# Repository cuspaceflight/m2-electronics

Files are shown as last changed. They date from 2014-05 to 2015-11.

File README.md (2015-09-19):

# Martlet 2 Flight Computers

This repository contains the schematics, PCB designs and firmware for the
various electronic systems onboard Martlet 2.

## M2FC: Flight Computer
This PCB records sensor data to onboard storage and determines when to fire
pyrotechnic channels for staging and parachute release.

## M2R: Radio
This PCB receives GPS signals and transmits rocket telemetry (lat, lng, alt, 
max alt) over a satellite radio and 70cm radio link.

## Radio Link M2RL
Communicate between two M2FCs

## Firmware
### ChibiOS Instructions

```bash
$ git submodule update --init
$ cd ChibiOS/ext
$ unzip fatfs-0.9-patched.zip
$ cd ../os/various/fatfs_bindings
$ sed -i '/extern SDCDriver SDCD1;/d' fatfs_diskio.c
```

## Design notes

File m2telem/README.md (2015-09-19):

# M2 Telemetry Common Code

Functions to encode and decode M2 telemetry packets, and to transmit and 
receive framed packets.

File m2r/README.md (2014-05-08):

# Martlet 2 Radio Board

This PCB transmits rocket telemetry (lat, lng, alt, max alt) over a satellite
radio and 70cm radio link.

The satellite radio uses a RockBLOCK Iridium modem. The 70cm link will use an
NTX2b from Radiometrix with a standard 1/4 wave antenna, in a similar setup to
the usual HAB case.

There's some possibility for clever radio modes and coding to be used, but it
will depend on how much time is available.

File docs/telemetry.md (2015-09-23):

# Martet 2 Telemetry

Document version: 2.0

This document describes version 2 of the Martlet 2 telemetry packet format. 
Compared to version 1, the two halves (the data segment and the metadata 
segment) are switched, to accommodate a trailing checksum. The packet mode 
became _managed_, associated with a particular channel, rather than being 
specified in the packet itself. Origins and channel constants are unchanged.

## Packet Format

16 byte packets: 8 byte data, 8 byte footer.

    [  0  | DATA       ]\
    [  1  | DATA       ] |
    [  2  | DATA       ] |
    [  3  | DATA       ] |- User data. Might be an 8-char string or an int64 or
    [  4  | DATA       ] |  two floats or four int16s or whatever else MODE
    [  5  | DATA       ] |  indicates.
    [  6  | DATA       ] |
    [  7  | DATA       ]/
    [  8  | TIMESTAMP  ]\
    [  9  | TIMESTAMP  ] |- A 32 bit unsigned timestamp that runs at the system
    [ 10  | TIMESTAMP  ] |  clock frequency so will overflow fairly often.
    [ 11  | TIMESTAMP  ]/
    [ 12  | METADATA   ]--- Origin of data and reserved bits.
    [ 13  | CHANNEL    ]--- Data channel.
    [ 14  | CHECKSUM L ]\
    [ 15  | CHECKSUM U ]/-- Verify packet contents.

## Metadata

The metadata byte describes the original source of a telemetry packet in the 
lower four bits. The upper four bits are reserved.

### Packet Origins

    0   RESERVED
    1   M2FC BODY
    2   M2FC NOSE
    3   M2R
    F   Groundstation

## Channel

The channel byte describes what data this packet contains. The `mode`
referenced in the channel table refers to one of the data formats described in
the `Data` section.

### Packet Channels

    Channel  Mode  Description
    -------------------------------------------------------------
    0x0            SYSTEM
       0     0      Initialisation message, contains the origin string
       1     0      Firmware version, as Git commit hash
       2     8      Statistics: [CPU_usage uSD_duty 0 0 0 0 0 0 0]
       3     8      Status 1: [M2FCBODY M2FCNOSE M2R 0 0 0 0 0]
       4     8      Status 2: [ADC LG_Accel HG_Accel Baro Gyro Magno Pyro uSD]
       5     8      Status 3: [SE MC Datalogging Config 0 0 0 0]
       6     8      Status 4: [RockBLOCK Radio GPS 0 0 0 0 0]

    0x1            CALIBRATION
       0     4      Timestamp frequency  [f 0]
       1     5      Low-G accelerometer  [axis gravity-magnitude 0 0]
       2     5      High-G accelerometer [axis gravity-magnitude 0 0]
       3     6      Barometer            [d0 c1 c2 c3]
       4     6      Barometer            [c4 c5 c6 d7]

    0x2            INTERTIAL MEASUREMENT
       0     5      Low-G accelerometer  [x y z 0]
       1     5      High-G accelerometer [x y z 0]
       2     3      Barometer            [pressure temperature]
       3     5      Rate gyroscope       [x y z 0]
       4     5      Magnetometer         [x y z 0]

    0x3            EXTERNAL SENSORS
       0     5      Battery voltage [millivolts 0 0 0]
       1     5      Strain gauges   [ch1 ch2 ch3 0]
       2     5      Thermocouples   [ch1 ch2 ch3 0]

    0x4            STATE MACHINES
       0     3      Mission Control [old_state new_state]

    0x5            STATE ESTIMATION
       0     9      Prediction output  I     [dt       height]
       1     9      Prediction output II     [velocity acceleration]
       2     9      Pressure measurement     [sensor   estimate]
       3     9      Acceleration measurement [sensor   estimate]

    0x6            PYROTECHNICS
       0     5      Continuity results [ch1 ch2 ch3 0]
       1     5      Fired              [ch1 ch2 ch3 0]

    0x7            LOCATION
       0     8      GPS Time       [year_l year_h month day hour min sec valid]
       1     3      GPS Position   [latitude longitude]
       2     3      GPS Altitude   [height height_msl]
       3     7      GPS Status     [fix_type flags num_sv 0 0 0 0 0]

;qa
## Checksum

CRC16-CCITT with polynomial 0x1021 and initial value 0xFFFF, no 
post-processing. Stored little-endien.

## Data

Data formatting depends on channel, allocated in the channel table. Multi byte 
entries are stored little-endien.

### Packet Modes

    Mode  Type      Format   Description
    -------------------------------------------------------------
     0    char*      s8       Eight byte string
     1    int64_t    q        64 bit signed integer
     2    uint64_t   Q        64 bit unsigned integer
     3    int32_t    ii       Two 32bit signed integers
     4    uint32_t   II       Two 32bit unsigned integers
     5    int16_t    hhhh     Four 16bit signed integers
     6    uint16_t   HHHH     Four 16bit unsigned integers
     7    int8_t     bbbbbbbb Eight 8bit signed integers
     8    uint8_t    BBBBBBBB Eight 8bit unsigned integers
     9    float      ff       Two 32bit single precision floats
     10   double     d        One 64bit double precision float

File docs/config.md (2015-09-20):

# Martlet 2 Config Files

Configuration settings are saved in a file named `config.txt` in the root of 
the SD card. Each line is one `key=value` pair, with values interpreted as 
either integers or floating point numbers. Bools should be specified as 0 or 1. 
Ints are all unsigned (in other words, non-negative, >= 0).

Configuration keys must be *in order* and exactly as follows:

Key              | Type  | Description
-----------------|-------|-----------------------------------------------------
accel_axis       | Int   | Which accelerometer axis is 'up', 0=x 1=y 2=z
pyro_firetime    | Int   | Time in milliseconds to fire pyros
pyro_1           | Int   | Pyro channel 1 usage: 0=unused 1=drogue 2=main
pyro_2           | Int   | Pyro channel 2 usage: 0=unused 1=drogue 2=main
pyro_3           | Int   | Pyro channel 3 usage: 0=unused 1=drogue 2=main
ignition_accel   | Int   | Acceleration threshold for detecting motor ignition, in m/s/s
burnout_time     | Int   | Time limit on motor burn duration, in milliseconds
apogee_time      | Int   | Time since burnout after which apogee is considered to have been reached, in milliseconds
main_altitude    | Int   | Altitude below which to release the main parachute, in metres AGL
main_time        | Int   | Time since apogee at which to release the main parachute, in milliseconds
landing_time     | Int   | Time since apogee at which to consider the rocket landed, in milliseconds
use_adc          | Bool  | 1 to read the ADCs, 0 to disable
use_magno        | Bool  | 1 to read the magno, 0 to disable
use_gyro         | Bool  | 1 to read the gyro, 0 to disable

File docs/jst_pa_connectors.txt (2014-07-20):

HEADER

02 SIDE S02B-PASK-2 1830747
03 SIDE S03B-PASK-2 1830748
04 SIDE S04B-PASK-2 1830749     RS: 512-8484

02 TOP  B02B-PASK   1830733
03 TOP  B03B-PASK   1830735
04 TOP  B04B-PASK   1830737

HOUSING

02 PAP-02V-S        1830726
03 PAP-03V-S        1830728
04 PAP-04V-S        1830729

CRIMP PIN

SPHD-001T-P0.5                  RS: 688-1381

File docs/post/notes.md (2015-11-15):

# M2 Electronics Postmortem Documentation: Planning Notes

## Structure

1. Introduction, Scope, Objectives
1. Hardware Design Review
1. Hardware Manufacture Review
1. Firmware Design Review
1. Firmware Implementation Review
1. Performance Analysis
1. Bugs and Other Issues
1. Lessons Learnt & Recommendations
1. Conclusions

## Structure Take 2

1. Summary
    1. Brief overview
    1. Key successes
    1. Key problems
    1. Key takeaways
1. Introduction
    1. Martlet 2 Overview
    1. Report scope and goals
    1. Project objectives
1. Avionics Overview
    1. Custom Hardware
        1. M2FC
        1. M2R
        1. M2RL
        1. M2PA
        1. JOEY Tracker
    1. Other Electronics
        1. RockBLOCK
        1. PerfectFlite
        1. Cameras
    1. Other Components
        1. Metrons
        1. Strain gauges
        1. Thermocouples
        1. Battery cases
        1. Arming switches
        1. Status LEDs
        1. Antennas
    1. Interconnection
1. Project Management
    1. Time management
    1. Collaboration
    1. Prioritisaton and Feature Freeze
1. System Review
1. Hardware Review
    1. Technology Choices (KiCAD)
    1. Design Procedure
    1. M2FC
        1. Analogue
        1. Pyrotechnics
        1. IMU
        1. SD Card
        1. Off-board integrations
    1. M2R
        1. Radio
        1. GPS
        1. RockBLOCK
        1. Buzzer
    1. M2RL
    1. M2PA
    1. Arming System
    1. Power System
    1. Other Electronics
        1. RockBLOCK
        1. PerfectFlite
        1. Cameras
    1. Other Components
        1. Metrons
        1. Strain gauges
        1. Thermocouples
        1. Battery cases
        1. Arming switches
        1. Status LEDs
        1. Antennas
    1. Interconnections
        1. JST PA
        1. Spec 55
        1. Radio links
    1. Manufacture
        1. Issues Encountered
    1. Testing
1. Software Review
    1. Technology Choices (C, git, ChibiOS)
    1. Reliability Management
        1. Watchdogs
        1. Hardware error handling
    1. Drivers
    1. Calibration
    1. Flight state machine
        1. Safety Timeouts
        1. Ignition Detection
    1. Status reporting and collection
    1. Telemetry collection and forwarding/storage
    1. Software interfaces
    1. Testing
    1. Ground station software
    1. Revision Control / Release Process
1. Integration Review
    1. Mounting
    1. Enclosures
    1. Switches and LEDs
    1. Cameras
    1. Antennas
    1. Cabling
    1. Sensors
1. Launch Retrospective
    1. Missing Features
        1. IMU Magno/Gyro
        1. ADC recording
        1. M2RL
    1. Asssembly
    1. Performance
        1. Radio
        1. Datalogging
        1. Sensors
        1. State estimation
    1. Issues Encountered
        1. No RockBLOCK signal while in enclosure
        1. Accidental body Metron firing in assembly
        1. Arming switch high up
        1. Arming switch behind launch rail
        1. Radio not enabled, requiring reprogramming
        1. Key breaking apart
        1. Keyswitch breaking off
        1. LED breaking off
        1. Upright on arming requirement
        1. No safety timeout
        1. Sensitive ignition detection
        1. Early body Metron firing while on pad
        1. SD cards lost
1. Conclusions & Recommendations

## Thoughts To Include
Per section: Overview, Performance, Issues, Lessons Learnt

## Links

GitHub repo: https://github.com/cuspaceflight/m2-electronics
Photos: https://www.flickr.com/photos/randomskk/albums/72157645881007740

## Thoughts drop

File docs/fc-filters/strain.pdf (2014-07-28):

## Filter Wizard

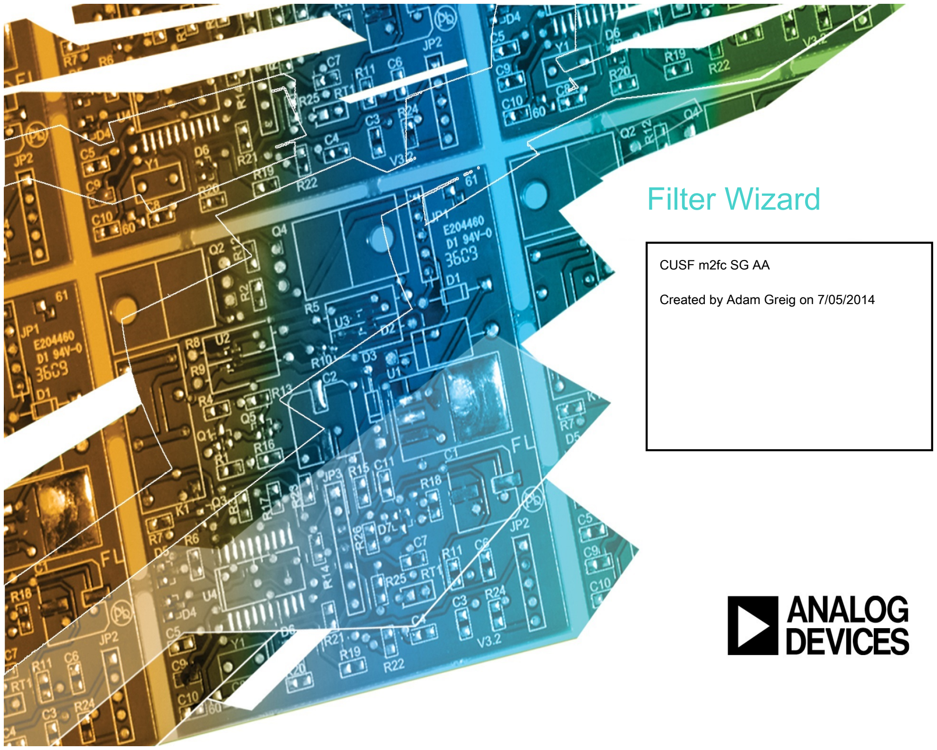
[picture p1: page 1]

CUSF m2fc SG AA

Created by Adam Greig on 7/05/2014

## Filter Wizard Design Report

Filter Requirements for Low-Pass, 4th order Butterworth Specifications: Optimize for Noise, +Vs= 3.3, -Vs= 0
Gain: 0 dB
Passband: -3dB at 2kHz
Stopband: -55dB at 10kHz
Component Tolerances: Capacitor = 10%; Resistor = 1%; Inductor = 5%; Op Amp GBW = 20% BOM: refer to BOM.csv file

Magnitude(dB)

Magnitude(Volts per Volt)

Phase(degrees)

Phase(radians)

Group Delay

Phase Delay

Step Response

Noise

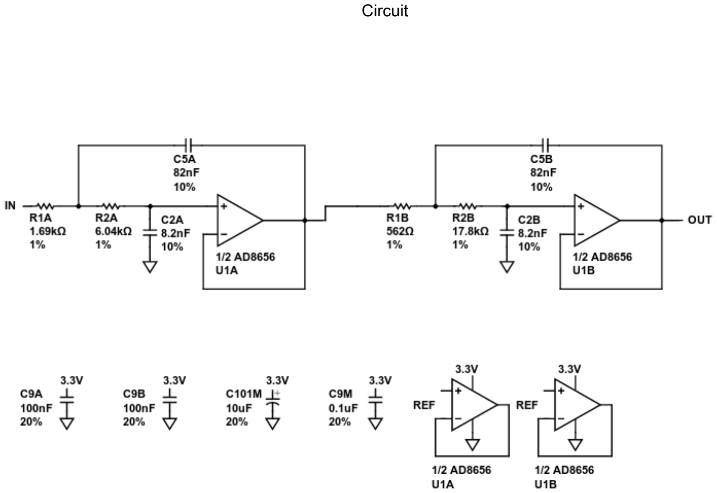
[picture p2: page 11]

Circuit

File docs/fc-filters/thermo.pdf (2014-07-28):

## Filter Wizard

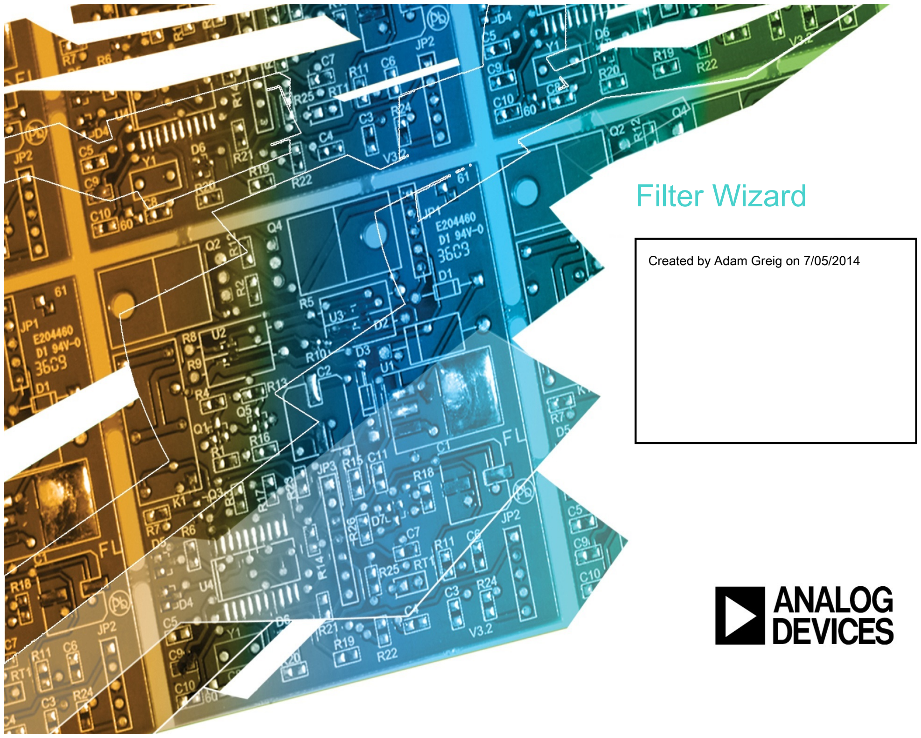
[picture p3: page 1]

Created by Adam Greig on 7/05/2014

## Filter Wizard Design Report

Filter Requirements for Low-Pass, 4th order Butterworth Specifications: Optimize for Specific Components, +Vs= 3.3, -Vs= 0 Gain: 0 dB
Passband: -3dB at 300Hz
Stopband: -40dB at 1kHz
Component Tolerances: Capacitor = 5%; Resistor = 1%; Inductor = 5%; Op Amp GBW = 20% BOM: refer to BOM.csv file

Magnitude(dB)

Magnitude(Volts per Volt)

Phase(degrees)

Phase(radians)

Group Delay

Phase Delay

Step Response

Noise

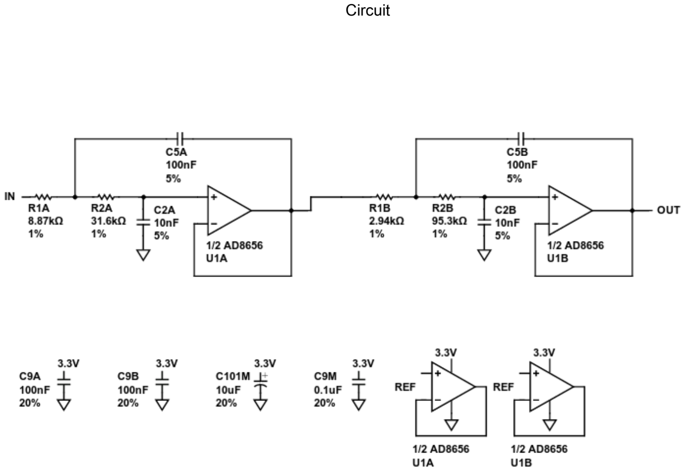
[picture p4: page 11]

Circuit

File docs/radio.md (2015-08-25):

# Martlet 2 Radio Protocol

Document version: 1.1

This document describes the physical and data link level radio protocol for 
Martlet 2. See the telemetry documentation for description of the application 
layer data packets.

## Physical Layer

Martlet 2 is equipped with a FSK radio module whose carrier frequency is 
controlled by the input voltage. However its primary telemetry downlink is via 
BPSK data, with a CW/Morse identification mode.

### Telemetry Downlink Mode

While downlinking telemetry packets, the following settings apply:

-                               |- 
--------------------------------|---------------
Nominal Carrier Frequency       | 434.650MHz
Modulation                      | BPSK
Bit rate                        | 2000 bps

### Identification Mode

In compliance with FCC 97.119 b 3, Martlet 2 will also identify itself and its 
data mode by a CW transmission, repeated twice. The transmitted message is:

    AD6AM/AM AD6AM/AM MARTLET 2 CUSF.CO.UK/M2R

-                               |-
--------------------------------|---------------
Nominal Carrier Frequency       | 434.650MHz
Modulation                      | Morse OOK
Speed                           | 20 wpm

## Data Link Layer

16 byte application packets are first randomised by combining with an LFSR of 
polynomial `x^8 + x^6 + x^4 + x^3 + x^2 + x^1 + 1`. This ensures sufficient 
transitions in the transmitted data stream and aids in balancing the 
transmitted spectrum. For further details see CCSDS 231.0-B-2 section 5.

Randomised application packets are then encoded with the systematic (256,128) 
LDPC code specified in CCSDS 231.1-O-1. The resulting codewords are transmitted 
left bit first, which corresponds to the most significant bit in the lowest 
(first) byte of the application payload.

Each codeword is then prefixed with the 16 bit synchronisation pattern 
`1110101110010000`, transmitted left bit first.

## Radio Sequencing

The radio follows this sequence on power-up:

1. Carrier enabled
2. If necessary, radio enters identification mode and repeats identification 
   message two times. Identification occurs once on startup and at least every 
   ten minutes thereafter.
3. Radio transitions to telemetry downlink mode and transmits a brief 
   unmodulated carrier.
4. Carrier modulated with repeating 1010 preamble for 16 bit periods
5. Data frame transmitted, starting with leading 1 in synchronisation pattern,
   ending with final (rightmost) parity bit of codeword.
6. Up to fifteen further frames transmitted starting with synchronisation 
   pattern, with no additional preamble.
7. Go to (2).

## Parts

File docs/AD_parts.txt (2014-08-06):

PART                QTY COST    SAMPLED

ADP3335ARMZ-3.3RL7  3   1.07
ADP3338AKCZ-5-R7    1   2.24
ADUM1201CRZ         5   2.85    2 SAMPLED 2014-08-04
ADUM5201CRWZ        2   8.80    2 SAMPLED 2014-07-20
ADL5324ARKZ-R7      1   7.28    2 SAMPLED 2014-07-20
ADXL375BCCZ         2   7.45    2 SAMPLED 2014-07-20
ADXL345BCCZ         2   5.97    1 SAMPLED 2014-08-03
AD8226ARMZ          6   2.45    1 SAMPLED 2014-08-03, 2 SAMPLED 2014-08-04
AD8541AKSZ-REEL7    6   0.64
AD8656ARMZ          12  2.72    1 SAMPLED 2014-08-03, 2 SAMPLED 2014-08-04
AD8495CRMZ          6   6.52    2 SAMPLED 2014-07-20, 1 SAMPLED 2014-08-03 (BACKORDER TIL SEPT 9), 2 SAMPLED 2014-08-04

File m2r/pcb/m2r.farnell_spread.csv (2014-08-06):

number | comment | name | stock | price | qty | cost | url
2141424 | 2 m2r:R0402 R3 | MULTICOMP - MC00625W040212R0 - RESISTOR, 2R, 0.063W, 1%, 0402 | 8,075 | 0.022 | 1 | 0.022 | http://onecall.farnell.com/_/_/_/dp/2141424
2063945 | 8M m2r:HC49S X10 | FOX ELECTRONICS - FOXSLF/080-20 - CRYSTAL, 8.0MHZ, 20PF | 683 | 0.32 | 1 | 0.32 | http://onecall.farnell.com/_/_/_/dp/2063945
1608592 | SMA m2r:SMA-142-0701-801 P7 | EMERSON CONNECTIVITY/JOHNSON - 142-0701-801 - RF COAXIAL, SMA, STRAIGHT JACK, 50OHM | 125 | 4.94 | 1 | 4.94 | http://onecall.farnell.com/_/_/_/dp/1608592
2211068 | 10µ m2r:C1206 C18 | TDK - CGA5L1X7R1E106K160AC - CAP, MLCC, X7R, 10UF, 25V, 1206 | 953 | 0.65 | 1 | 0.65 | http://onecall.farnell.com/_/_/_/dp/2211068
2333614 | 6k8 m2r:R0603 R6 | BOURNS - CR0603-FX-6801ELF - RESISTOR THICK FILM, 6.8KOHM, 1%, 0603 | 1,463 | 0.018 | 1 | 0.018 | http://onecall.farnell.com/_/_/_/dp/2333614
BT01732 | BAT BOX None X1 | BULGIN - BX0027 - BATTERY HOLDER ENCLOSED FOUR X AA | 75 | 6.72 | 1 | 6.72 | http://onecall.farnell.com/_/_/_/dp/BT01732
2290330 | YELLOW m2r:LED0603 D3 D4 D6 D5 | KINGBRIGHT - KP-1608SYCK - LED, 0603, 150MCD, YELLOW | 15,179 | 0.054 | 4 | 0.216 | http://onecall.farnell.com/_/_/_/dp/2290330
2290329 | RED m2r:LED0603 D1 D2 | KINGBRIGHT - KP-1608SURCK - LED, 0603, 230MCD, RED | 65,670 | 0.054 | 2 | 0.108 | http://onecall.farnell.com/_/_/_/dp/2290329
2331989 | 100 m2r:R0603 R14 R8 R9 R7 R10 R12 R11 R13 R5 R4 | TE CONNECTIVITY - CRGH0603F100R - RESISTOR, POWER, 100R, 0.2W, 1%, 0603 | 4,737 | 0.008 | 10 | 0.08 | http://onecall.farnell.com/_/_/_/dp/2331989
2099794 | ADL5324 m2r:SOT89-3 IC7 | ANALOG DEVICES - ADL5324ARKZ-R7 - RF, AMP, 400MHZ-4GHZ, 0.5W, SOT89 | 834 | 7.28 | 1 | 7.28 | http://onecall.farnell.com/_/_/_/dp/2099794
1885332 | 10p m2r:C0402 C19 | JOHANSON TECHNOLOGY - 500R07S100GV4T - CAP, RF, C0G/NP0, 10PF, 50V, 0402 | 10,465 | 0.235 | 1 | 0.235 | http://onecall.farnell.com/_/_/_/dp/1885332
1885324 | 6p2 m2r:C0402 C22 | JOHANSON TECHNOLOGY - 500R07S6R2CV4T - CAP, RF, C0G/NP0, 6.2PF, 50V, 0402 | 4,870 | 0.113 | 1 | 0.113 | http://onecall.farnell.com/_/_/_/dp/1885324
1830729 | HOUSING None X5 X6 X7 | JST (JAPAN SOLDERLESS TERMINALS) - PAP-04V-S - HOUSING, CRIMP, RECEPTACLE, 2MM, 4WAY | 37,852 | 0.10 | 3 | 0.30000000000000004 | http://onecall.farnell.com/_/_/_/dp/1830729
2368169 | CGA0402MLC-12G m2r:R0402 D8 D7 D9 D10 D11 | BOURNS - CGA0402MLC-12G - ESD SUPPRESSOR, 0402, 12V, 0.2PF | 8,890 | 0.138 | 5 | 0.6900000000000001 | http://onecall.farnell.com/_/_/_/dp/2368169
2331727 | 1k m2r:R0603 R2 | TE CONNECTIVITY - CRGH0603J1K0 - RESISTOR, POWER, 1K0, 0.2W, 5%, 0603 | 2,100 | 0.006 | 1 | 0.006 | http://onecall.farnell.com/_/_/_/dp/2331727
1078200 | ADuM1201 m2r:SOIC8 IC5 IC3 IC4 | ANALOG DEVICES - ADUM1201ARZ - DIGITAL ISOLATOR, 2CH, 150NS, SOIC8 | 999 | 2.46 | 3 | 7.38 | http://onecall.farnell.com/_/_/_/dp/1078200
2285660 | 5n6 m2r:L0402 L3 | COILCRAFT - 0402CS-5N6XGLU - INDUCTOR, RF, 5.6NH, 2%, 4.8GHZ, SMD | 296 | 0.894 | 1 | 0.894 | http://onecall.farnell.com/_/_/_/dp/2285660
1759055 | 15p m2r:C0603 C35 C36 | MULTICOMP - MC0603N150J500CT - CAP, MLCC, C0G/NP0, 15PF, 50V, 0603 | 47,738 | 0.008 | 2 | 0.016 | http://onecall.farnell.com/_/_/_/dp/1759055
2112704 | 10n m2r:C0603 C17 | TDK - C1608C0G1E103J - CAP, MLCC, C0G/NP0, 10NF, 25V, 0603 | 3,907 | 0.133 | 1 | 0.133 | http://onecall.farnell.com/_/_/_/dp/2112704
1885343 | 20p m2r:C0402 C21 C20 | JOHANSON TECHNOLOGY - 500R07S200GV4T - CAP, RF, C0G/NP0, 20PF, 50V, 0402 | 6,525 | 0.054 | 2 | 0.108 | http://onecall.farnell.com/_/_/_/dp/1885343
1830726 | HOUSING None X3 X4 X9 | JST (JAPAN SOLDERLESS TERMINALS) - PAP-02V-S - HOUSING, CRIMP, RECEPTACLE, 2MM, 2WAY | 24,617 | 0.107 | 3 | 0.321 | http://onecall.farnell.com/_/_/_/dp/1830726
1142488 | RG LED None X8 | KINGBRIGHT - L-937EGW - LED, 3MM, HE-RED/GRN | 24,541 | 0.33 | 1 | 0.33 | http://onecall.farnell.com/_/_/_/dp/1142488
2285957 | 120n m2r:L0603 L1 | COILCRAFT - 0603CS-R12XGLU - INDUCTOR, RF, 120NH, 2%, 1.3GHZ, SMD | 83 | 0.64 | 1 | 0.64 | http://onecall.farnell.com/_/_/_/dp/2285957
1865153 | ALM-2712 m2r:ALM-2712 IC9 | AVAGO TECHNOLOGIES - ALM-2712-BLKG - FILTER, FRONT END, LNA/GPS, 12MCOB | 129 | 2.09 | 1 | 2.09 | http://onecall.farnell.com/_/_/_/dp/1865153
2376929 | ADP3333 m2r:MSOP8 IC11 | ANALOG DEVICES - ADP3333ARMZ-2.5-R7 - 300MA FIXED ANYCAP LDO | 859 | 1.24 | 1 | 1.24 | http://onecall.farnell.com/_/_/_/dp/2376929
1651284 | ADP3338 m2r:SOT223 IC1 | ANALOG DEVICES - ADP3338AKCZ-5-R7. - LDO REG, 1A, RECISION 5V, SOT223 | 507 | 2.24 | 1 | 2.24 | http://onecall.farnell.com/_/_/_/dp/1651284
2285968 | 1n6 m2r:L0603 L2 | COILCRAFT - 0603CS-1N6XJLU - INDUCTOR, RF, 1.6NH, 5%,12.5GHZ, SMD | 210 | 0.505 | 1 | 0.505 | http://onecall.farnell.com/_/_/_/dp/2285968
1830747 | CONN_2 m2r:S02B-PASK-2 P1 P8 P2 | JST (JAPAN SOLDERLESS TERMINALS) - S02B-PASK-2 - HEADER, PA, 2WAY, SIDE, 2MM | 2,567 | 0.29 | 3 | 0.8699999999999999 | http://onecall.farnell.com/_/_/_/dp/1830747
2332016 | 10k m2r:R0603 R1 | TE CONNECTIVITY - CRGH0603F10K - RESISTOR, POWER, 10K, 0.2W, 1%, 0603 | 6,713 | 0.008 | 1 | 0.008 | http://onecall.farnell.com/_/_/_/dp/2332016
1759037 | 100n m2r:C0603 C14 C6 C2 C11 C3 C4 C15 C30 C31 C24 C25 C26 C27 C29 C34 C5 C1 | MULTICOMP - MC0603B104K250CT - CAP, MLCC, X7R, 100NF, 25V, 0603 | ERR | 0.006 | 17 | 0.10200000000000001 | http://onecall.farnell.com/_/_/_/dp/1759037
2067775 | ADP3335 m2r:MSOP8 IC2 | ANALOG DEVICES - ADP3335ARMZ-3.3 - IC, LDO REGULATOR, 0.5A, 6V, MSOP-8 | 675 | 1.07 | 1 | 1.07 | http://onecall.farnell.com/_/_/_/dp/2067775
149288 | ARM SW None X2 | BULGIN - VS0002 - VOLTAGE SELECTOR, 120/240V | ERR | 3.66 | 1 | 3.66 | http://onecall.farnell.com/_/_/_/dp/149288
2308436 | SWD m2r:FTSH-105-01-F-D-K P6 | SAMTEC - FTSH-105-01-L-D - CONNECTOR, HEADER, 1.27MM, PCB, 10WAY | 165 | 1.81 | 1 | 1.81 | http://onecall.farnell.com/_/_/_/dp/2308436
2333361 | STM32F303C m2r:LQFP48 IC10 | STMICROELECTRONICS - STM32F303CBT7 - MCU, 32BIT, CORTEX-M4, 72MHZ, LQFP-48 | 269 | 5.48 | 1 | 5.48 | http://onecall.farnell.com/_/_/_/dp/2333361
1759088 | 1n m2r:C0603 C12 | MULTICOMP - MC0603B102K500CT - CAP, MLCC, X7R, 1NF, 50V, 0603 | 82,590 | 0.006 | 1 | 0.006 | http://onecall.farnell.com/_/_/_/dp/1759088
2333026 | 10µ m2r:C0603 C23 | AVX - TAJB106M016RNJ - CAP, TANT, 10UF, 16V, CASE B | 6,648 | 0.125 | 1 | 0.125 | http://onecall.farnell.com/_/_/_/dp/2333026
2320817 | 2µ2 m2r:C0603 C7 C8 C9 C10 C13 C33 C32 | MULTICOMP - MC0603X225K100CT - CAP, MLCC, X5R, 2.2UF, 10V, 0603 | 18,395 | 0.018 | 7 | 0.126 | http://onecall.farnell.com/_/_/_/dp/2320817
1658211 | 1µ m2r:C0603 C28 | AVX - TAJR105K025RNJ - CAP, TANT, 1UF, 25V, CASE R | 943 | 0.37 | 1 | 0.37 | http://onecall.farnell.com/_/_/_/dp/1658211
1327627 | 100p m2r:C0402 C16 | AVX - 04025A101JAT2A - CAP, MLCC, C0G/NP0, 100PF, 50V, 0402 | 78,414 | 0.057 | 1 | 0.057 | http://onecall.farnell.com/_/_/_/dp/1327627

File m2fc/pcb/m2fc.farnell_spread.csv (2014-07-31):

number | comment | name | stock | price | qty | cost | url
2346895 | 1µ m2fc:C0603 C117 C608 C619 C630 | TDK - C1608X7R1A105K080AC - CAP, MLCC, X7R, 1UF, 10V, 0603 | 1,950 | 0.0351 | 4 | 0.1404 | http://onecall.farnell.com/_/_/_/dp/2346895
2332025 | 47k m2fc:R0603 R103 R104 R105 R106 R107 | TE CONNECTIVITY - CRGH0603F47K - RESISTOR, POWER, 47K, 0.2W, 1%, 0603 | 4,830 | 0.008 | 5 | 0.04 | http://onecall.farnell.com/_/_/_/dp/2332025
1833803 | 4µ7 m2fc:C0603 C314 | AVX - 06036D475KAT2A - CAP, MLCC, X5R, 4.7UF, 6.3V, 0603 | 29,215 | 0.163 | 1 | 0.163 | http://onecall.farnell.com/_/_/_/dp/1833803
2368169 | CGA0402MLC-12G m2fc:R0402 D101 D102 D201 D202 D203 D204 D205 D206 D406 D407 D502 D504 D506 D601 D602 D603 D604 D605 D606 | BOURNS - CGA0402MLC-12G - ESD SUPPRESSOR, 0402, 12V, 0.2PF | 8,890 | 0.138 | 19 | 2.6220000000000003 | http://onecall.farnell.com/_/_/_/dp/2368169
1414605 | 1n m2fc:C0603 C105 C125 | KEMET - C0603C102J5GACTU - CAP, MLCC, C0G/NP0, 1NF, 50V, 0603 | 3,714 | 0.032 | 2 | 0.064 | http://onecall.farnell.com/_/_/_/dp/1414605
1667759 | SWD m2fc:FTSH-105-01-F-D-K P104 | SAMTEC - FTSH-105-01-L-DV - HEADER, 1.27MM, SMD, 10WAY | 2,038 | 2.08 | 1 | 2.08 | http://onecall.farnell.com/_/_/_/dp/1667759
2211164 | 10µ m2fc:C0603 C109 C107 C204 C205 C206 C213 C217 C218 C219 C226 C230 C231 C232 C239 C303 C306 C309 C402 C401 C602 C605 C613 C616 C627 C624 | TDK - C1608X5R1A106K080AC - CAP, MLCC, X5R, 10UF, 10V, 0603 | 325 | 0.32 | 25 | 8.0 | http://onecall.farnell.com/_/_/_/dp/2211164
BT01732 | BAT BOX None U101 | BULGIN - BX0027 - BATTERY HOLDER ENCLOSED FOUR X AA | 76 | 6.72 | 1 | 6.72 | http://onecall.farnell.com/_/_/_/dp/BT01732
2067807 | AD8495 m2fc:MSOP8 IC601 IC603 IC605 | ANALOG DEVICES - AD8495CRMZ - THERMOCOUPLE, W/COMP, 8MSOP | 105 | 6.52 | 3 | 19.56 | http://onecall.farnell.com/_/_/_/dp/2067807
1877590 | 10k 0.05% m2fc:R0603 R202 R208 R210 R216 R218 R224 | VISHAY DRALORIC - TNPU0603 10K 0,05 % T-16 E52 E3 - RESISTOR, HI PREC, 0603, 10K, 0.05% | 765 | 1.33 | 6 | 7.98 | http://onecall.farnell.com/_/_/_/dp/1877590
1759055 | 15p m2fc:C0603 C123 C121 | MULTICOMP - MC0603N150J500CT - CAP, MLCC, C0G/NP0, 15PF, 50V, 0603 | 47,788 | 0.008 | 2 | 0.016 | http://onecall.farnell.com/_/_/_/dp/1759055
1759037 | 100n m2fc:C0603 C113 C112 C110 C111 C122 C103 C108 C114 C115 C116 C102 C209 C210 C211 C212 C222 C223 C224 C225 C235 C236 C237 C238 C301 C302 C304 C305 C310 C308 C307 C403 C404 C407 C405 C406 C408 C501 C502 C503 C601 C604 C612 C615 C623 C626 | MULTICOMP - MC0603B104K250CT - CAP, MLCC, X7R, 100NF, 25V, 0603 | ERR | 0.006 | 45 | 0.27 | http://onecall.farnell.com/_/_/_/dp/1759037
2116838 | 31.6k m2fc:R0603 R603 R610 R617 | TE CONNECTIVITY - RP73PF1J31K6BTDF - RESISTOR, 0603, 0.17W, 31K6, 0.1%, 25PPM | 1,020 | 0.209 | 3 | 0.627 | http://onecall.farnell.com/_/_/_/dp/2116838
1894738 | MOSFET_P m2fc:SOT-23-MOSFET Q501 Q503 Q505 | NXP - NX2301P - MOSFET, P CH, 20V, 2A, SOT23 | 17,562 | 0.094 | 3 | 0.28200000000000003 | http://onecall.farnell.com/_/_/_/dp/1894738
2290329 | RED m2fc:LED0603 D401 D408 | KINGBRIGHT - KP-1608SURCK - LED, 0603, 230MCD, RED | 65,837 | 0.054 | 2 | 0.108 | http://onecall.farnell.com/_/_/_/dp/2290329
2116811 | 17.8k m2fc:R0603 R207 R215 R223 | TE CONNECTIVITY - RP73PF1J17K8BTDF - RESISTOR, 0603, 0.17W, 17K8, 0.1%, 25PPM | 295 | 0.202 | 3 | 0.6060000000000001 | http://onecall.farnell.com/_/_/_/dp/2116811
2116779 | 8.87k m2fc:R0603 R602 R609 R616 | TE CONNECTIVITY - RP73PF1J8K87BTDF - RESISTOR, 0603, 0.17W, 8K87, 0.1%, 25PPM | 40 | 0.211 | 3 | 0.633 | http://onecall.farnell.com/_/_/_/dp/2116779
1830729 | HOUSING None U201 U202 U203 U401 U403 | JST (JAPAN SOLDERLESS TERMINALS) - PAP-04V-S - HOUSING, CRIMP, RECEPTACLE, 2MM, 4WAY | 38,352 | 0.10 | 5 | 0.5 | http://onecall.farnell.com/_/_/_/dp/1830729
1833876 | 10n m2fc:C0603 C311 | AVX - 06031C103JAT2A - CAP, MLCC, X7R, 10NF, 100V, 0603 | 13,110 | 0.177 | 1 | 0.177 | http://onecall.farnell.com/_/_/_/dp/1833876
2067775 | ADP3335 m2fc:MSOP8 IC101 IC103 | ANALOG DEVICES - ADP3335ARMZ-3.3 - IC, LDO REGULATOR, 0.5A, 6V, MSOP-8 | 675 | 1.07 | 2 | 2.14 | http://onecall.farnell.com/_/_/_/dp/2067775
2320817 | 2µ2 m2fc:C0603 C106 C104 C101 C119 C120 C124 C126 | MULTICOMP - MC0603X225K100CT - CAP, MLCC, X5R, 2.2UF, 10V, 0603 | 18,425 | 0.018 | 7 | 0.126 | http://onecall.farnell.com/_/_/_/dp/2320817
1349646 | DIODESCH m2fc:SOD323 D501 D503 D505 | NXP - 1PS76SB40 - DIODE, SCHOTTKY, SOD323 | 27,269 | 0.066 | 3 | 0.198 | http://onecall.farnell.com/_/_/_/dp/1349646
2331989 | 100 m2fc:R0603 R108 R407 R406 R401 R402 R403 R404 R405 R408 R502 R503 R509 R510 R516 R517 | TE CONNECTIVITY - CRGH0603F100R - RESISTOR, POWER, 100R, 0.2W, 1%, 0603 | 4,837 | 0.008 | 15 | 0.12 | http://onecall.farnell.com/_/_/_/dp/2331989
1971743 | HMC5883L m2fc:HMC5883L IC304 | HONEYWELL M&PS - HMC5883L-TR - IC, DIGITAL COMPASS, 3 AXIS, 16 PIN | 12,607 | 4.79 | 1 | 4.79 | http://onecall.farnell.com/_/_/_/dp/1971743
2332016 | 10k m2fc:R0603 R101 R301 R302 R305 R303 R308 R306 R304 R307 R507 R506 R501 R504 R514 R513 R508 R511 R521 R520 R515 R518 | TE CONNECTIVITY - CRGH0603F10K - RESISTOR, POWER, 10K, 0.2W, 1%, 0603 | 6,723 | 0.008 | 21 | 0.168 | http://onecall.farnell.com/_/_/_/dp/2332016
1830749 | CONN_4 m2fc:S04B-PASK-2 P201 P202 P203 P401 P403 | JST (JAPAN SOLDERLESS TERMINALS) - S04B-PASK-2 - HEADER, PA, 4WAY, SIDE, 2MM | ERR | 0.36 | 5 | 1.7999999999999998 | http://onecall.farnell.com/_/_/_/dp/1830749
1830747 | CONN_2 m2fc:S02B-PASK-2 P102 P103 P101 P402 P501 P502 P503 P601 P602 P603 | JST (JAPAN SOLDERLESS TERMINALS) - S02B-PASK-2 - HEADER, PA, 2WAY, SIDE, 2MM | 2,567 | 0.29 | 10 | 2.9 | http://onecall.farnell.com/_/_/_/dp/1830747
1078200 | ADuM1201 m2fc:SOIC8 IC402 | ANALOG DEVICES - ADUM1201ARZ - DIGITAL ISOLATOR, 2CH, 150NS, SOIC8 | 999 | 2.46 | 1 | 2.46 | http://onecall.farnell.com/_/_/_/dp/1078200
2116889 | 95.3k m2fc:R0603 R605 R612 R619 | TE CONNECTIVITY - RP73PF1J95K3BTDF - RESISTOR, 0603, 0.17W, 95K3, 0.1%, 25PPM | 555 | 0.209 | 3 | 0.627 | http://onecall.farnell.com/_/_/_/dp/2116889
2101329 | 8M m2fc:XTAL50x32 X101 | ABRACON - ABM3-8.000MHZ-D2Y-T - CRYSTAL, 8MHZ, 18PF, SMD | 8,367 | 1.16 | 1 | 1.16 | http://onecall.farnell.com/_/_/_/dp/2101329
1837433 | AD8541 m2fc:SC-70-5 IC203 IC206 IC209 | ANALOG DEVICES - AD8541AKSZ-R2 - IC, OP-AMP, 1MHZ, 0.92V/ us, SC-70-5 | 723 | 0.43 | 3 | 1.29 | http://onecall.farnell.com/_/_/_/dp/1837433
1827359 | AD8226 m2fc:MSOP8 IC201 IC204 IC207 | ANALOG DEVICES - AD8226ARMZ - IC, AMP, INST, R-R, LP, 13MA, 8MSOP | ERR | 2.45 | 3 | 7.3500000000000005 | http://onecall.farnell.com/_/_/_/dp/1827359
1830726 | HOUSING None U104 U103 U105 U404 U501 U502 U503 | JST (JAPAN SOLDERLESS TERMINALS) - PAP-02V-S - HOUSING, CRIMP, RECEPTACLE, 2MM, 2WAY | 24,617 | 0.107 | 7 | 0.749 | http://onecall.farnell.com/_/_/_/dp/1830726
2334075 | MICROSD m2fc:MICROSD U106 | MOLEX - 503182-1853 - CONNECTOR, MICRO SD, PUSH PUSH, 1.45MM | 796 | 0.694 | 1 | 0.694 | http://onecall.farnell.com/_/_/_/dp/2334075
2321755 | 1M m2fc:R0603 R607 R614 R621 | BOURNS - CR0603-FX-1004ELF - RESISTOR THICK FILM, 1MOHM, 1%, 0603 | 14,376 | 0.032 | 3 | 0.096 | http://onecall.farnell.com/_/_/_/dp/2321755
2362662 | MS5611-01BA03 m2fc:MS5611-01BA IC303 | MEASUREMENT SPECIALTIES - MS561101BA03-50 - SENSOR, BAROMETRIC, 0.01-1.2BAR, QFN-8 | 169 | 5.28 | 1 | 5.28 | http://onecall.farnell.com/_/_/_/dp/2362662
2067773 | ADuM5201 m2fc:SOIC16 IC401 | ANALOG DEVICES - ADUM5201CRWZ - ISOLATOR, W/DC-DC, 16SOIC | ERR | 8.80 | 1 | 8.8 | http://onecall.farnell.com/_/_/_/dp/2067773
1858055 | AD8656 m2fc:MSOP8 IC202 IC205 IC208 IC602 IC604 IC606 | ANALOG DEVICES - AD8656ARMZ - IC, OP AMP, 28MHZ, 8MSOP | 421 | 2.72 | 6 | 16.32 | http://onecall.farnell.com/_/_/_/dp/1858055
1853935 | ADXL345 m2fc:ADXL3x5 IC302 | ANALOG DEVICES - ADXL345BCCZ - IC, ACCELEROMETER, 3AXIS, 14LGA | 1,448 | 5.97 | 1 | 5.97 | http://onecall.farnell.com/_/_/_/dp/1853935
1867949 | 470n m2fc:C0603 C313 | AVX - 06033C474KAT2A - CAP, MLCC, X7R, 470NF, 25V, 0603 | 26,950 | 0.197 | 1 | 0.197 | http://onecall.farnell.com/_/_/_/dp/1867949
1142488 | RG LED None U402 | KINGBRIGHT - L-937EGW - LED, 3MM, HE-RED/GRN | 26,325 | 0.33 | 1 | 0.33 | http://onecall.farnell.com/_/_/_/dp/1142488
2116727 | 2.94k m2fc:R0603 R604 R611 R618 | TE CONNECTIVITY - RP73PF1J2K94BTDF - RESISTOR, 0603, 0.17W, 2K94, 0.1%, 25PPM | 240 | 0.202 | 3 | 0.6060000000000001 | http://onecall.farnell.com/_/_/_/dp/2116727
2116702 | 1.69k m2fc:R0603 R204 R212 R220 | TE CONNECTIVITY - RP73PF1J1K69BTDF - RESISTOR, 0603, 0.17W, 1K69, 0.1%, 25PPM | 575 | 0.211 | 3 | 0.633 | http://onecall.farnell.com/_/_/_/dp/2116702
2210859 | 8.2n m2fc:C0603 C207 C208 C220 C221 C233 C234 | TDK - CGA3E2C0G1H822J080AA - CAP, MLCC, C0G/NP0, 8.2NF, 50V, 0603 | 2,655 | 0.26 | 6 | 1.56 | http://onecall.farnell.com/_/_/_/dp/2210859
2116678 | 1k m2fc:R0603 R102 R201 R209 R217 R601 R606 R608 R613 R615 R620 | TE CONNECTIVITY - RP73PF1J1K0BTDF - RESISTOR, 0603, 0.17W, 1K0, 0.1%, 25PPM | 10 | 0.211 | 10 | 2.11 | http://onecall.farnell.com/_/_/_/dp/2116678
1872924 | L3G4200D m2fc:L3G4200D IC305 | STMICROELECTRONICS - L3G4200D - GYRO, MEMS, 3AXIS, 16LLGA, 16LGA | 321 | 7.20 | 1 | 7.2 | http://onecall.farnell.com/_/_/_/dp/1872924
2112704 | 10n m2fc:C0603 C118 C201 C214 C227 C609 C610 C620 C621 C631 C632 | TDK - C1608C0G1E103J - CAP, MLCC, C0G/NP0, 10NF, 25V, 0603 | 3,907 | 0.133 | 10 | 1.33 | http://onecall.farnell.com/_/_/_/dp/2112704
1510761 | MOSFET_N m2fc:SOT-23-MOSFET Q502 Q504 Q506 | NXP - 2N7002,215 - MOSFET,N CH, 60V,0.3A,SOT23 | 245,646 | 0.03 | 3 | 0.09 | http://onecall.farnell.com/_/_/_/dp/1510761
1577599 | 330 m2fc:R0603 R203 R211 R219 | PANASONIC - ERA3AEB331V - RESISTOR, 0603, 330R, 0.1%, 0.1W | 9,183 | 0.199 | 3 | 0.597 | http://onecall.farnell.com/_/_/_/dp/1577599
2211074 | 100n m2fc:C1206 C603 C611 C607 C606 C614 C622 C618 C617 C625 C633 C629 C628 | TDK - CGA5L2C0G1H104J160AA - CAP, MLCC, C0G/NP0, 100NF, 50V, 1206 | 11,747 | 0.48 | 12 | 5.76 | http://onecall.farnell.com/_/_/_/dp/2211074
1865539 | 82n m2fc:C0603 C203 C202 C216 C215 C229 C228 | KEMET - C0603C823K5RACTU - CAP, MLCC, X7R, 82NF, 50V, 0603 | 8,066 | 0.05 | 6 | 0.30000000000000004 | http://onecall.farnell.com/_/_/_/dp/1865539
1833865 | 220n m2fc:C0603 C312 | AVX - 06033C224KAT2A - CAP, MLCC, X7R, 220NF, 25V, 0603 | 38,875 | 0.211 | 1 | 0.211 | http://onecall.farnell.com/_/_/_/dp/1833865
2290330 | YELLOW m2fc:LED0603 D402 D403 D404 D405 | KINGBRIGHT - KP-1608SYCK - LED, 0603, 150MCD, YELLOW | 15,209 | 0.054 | 4 | 0.216 | http://onecall.farnell.com/_/_/_/dp/2290330
2361527 | ADXL375 m2fc:ADXL3x5 IC301 | ANALOG DEVICES - ADXL375BCCZ - ACCELEROMETER, 200G, LGA-14 | 371 | 7.45 | 1 | 7.45 | http://onecall.farnell.com/_/_/_/dp/2361527
2116652 | 562 m2fc:R0603 R206 R214 R222 | TE CONNECTIVITY - RP73PF1J562RBTDF - RESISTOR, 0603, 0.17W, 562R, 0.1%, 25PPM | 664 | 0.209 | 3 | 0.627 | http://onecall.farnell.com/_/_/_/dp/2116652
2328356 | 5 m2fc:PWR4318 R505 R512 R519 | BOURNS - PWR4318W5R00JE - RESISTOR WIREWOUND, 5OHM, 5%, SMD | 1,333 | 0.78 | 3 | 2.34 | http://onecall.farnell.com/_/_/_/dp/2328356
2116761 | 6.04k m2fc:R0603 R205 R213 R221 | TE CONNECTIVITY - RP73PF1J6K04BTDF - RESISTOR, 0603, 0.17W, 6K04, 0.1%, 25PPM | 189 | 0.211 | 3 | 0.633 | http://onecall.farnell.com/_/_/_/dp/2116761
2393648 | STM32F405VGT m2fc:LQFP100 IC102 | STMICROELECTRONICS - STM32F405VGT7 - MCU, 32BIT, CORTEX-M4, 168MHZ, LQFP-100 | 232 | 8.63 | 1 | 8.63 | http://onecall.farnell.com/_/_/_/dp/2393648
SW04244 | ARM SW None U102 | BULGIN - VS0002 - VOLTAGE SELECTOR, 120/240V | 21 | 2.55 | 1 | 2.55 | http://onecall.farnell.com/_/_/_/dp/SW04244

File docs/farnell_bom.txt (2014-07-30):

2285957, 1
2290330, 4
2331989, 10
2141424, 1
149288, 1
2368169, 5
1865153, 1
1830726, 3
2063945, 1
2333614, 1
2067775, 1
2333361, 1
2331727, 1
2285660, 1
2290329, 2
2376929, 1
1759055, 2
1885332, 1
2211068, 1
2320817, 7
1759037, 17
2099794, 1
1830747, 3
2333026, 1
1830729, 3
1651284, 1
1184194, 1
2285968, 1
1608592, 1
1078200, 3
2332016, 1
2308436, 1
1885343, 2
1142488, 1
1759088, 1
1885324, 1
1658211, 1
2112704, 1
1327627, 1
2116678, 10
1833803, 1
2067807, 3
2116761, 3
2210859, 6
1667759, 1
2290330, 4
1056832, 3
1142488, 1
2081363, 1
1858055, 6
2368169, 19
2393648, 1
1837433, 3
2361527, 1
2063945, 1
2067773, 1
2346569, 3
2067775, 1
1510761, 3
2117295, 3
2290329, 1
1759055, 2
2346895, 4
2328356, 3
2117134, 3
2116838, 3
2332025, 5
1894738, 3
2320817, 5
1759037, 45
1867949, 1
1971743, 1
1865539, 6
1657936, 24
1853935, 1
1830747, 10
1877590, 6
2116702, 3
1830726, 7
1872924, 1
1830729, 5
1414605, 1
1184194, 1
1078200, 1
2332016, 24
2362662, 1
2211074, 12
2331989, 14
2321755, 3
1827359, 3
2117211, 3
2116779, 3
1833876, 1
1577599, 3
2112704, 10
1833865, 1
149288, 1
2117373, 3
2116678, 10
1833803, 1
2067807, 3
2116761, 3
2210859, 6
1667759, 1
2290330, 4
1056832, 3
1142488, 1
2081363, 1
1858055, 6
2368169, 19
2393648, 1
1837433, 3
2361527, 1
2063945, 1
2067773, 1
2346569, 3
2067775, 1
1510761, 3
2117295, 3
2290329, 1
1759055, 2
2346895, 4
2328356, 3
2117134, 3
2116838, 3
2332025, 5
1894738, 3
2320817, 5
1759037, 45
1867949, 1
1971743, 1
1865539, 6
1657936, 24
1853935, 1
1830747, 10
1877590, 6
2116702, 3
1830726, 7
1872924, 1
1830729, 5
1414605, 1
1184194, 1
1078200, 1
2332016, 24
2362662, 1
2211074, 12
2331989, 14
2321755, 3
1827359, 3
2117211, 3
2116779, 3
1833876, 1
1577599, 3
2112704, 10
1833865, 1
149288, 1
2117373, 3

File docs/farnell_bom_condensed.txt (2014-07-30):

2116678, 20
1833865, 2
1837433, 6
2116761, 6
2210859, 12
2285957, 1
1667759, 2
2290330, 12
1877590, 12
1056832, 6
2141424, 1
149288, 3
1858055, 12
2368169, 43
2332025, 10
1865153, 1
1414605, 2
2361527, 2
2333361, 1
2333614, 1
2067775, 3
2063945, 3
2331727, 1
1894738, 6
2117295, 6
2067773, 2
2285660, 1
1830726, 17
1759055, 6
2346895, 8
2346569, 6
2117134, 6
1184194, 3
1142488, 3
1885332, 1
2393648, 2
2211068, 1
2067807, 6
2320817, 17
1759037, 107
1867949, 2
1971743, 2
1865539, 12
1657936, 48
2099794, 1
2333026, 1
1830747, 23
2116838, 6
2116702, 6
2290329, 4
1759088, 1
1872924, 2
1830729, 13
1651284, 1
1510761, 6
2376929, 1
1608592, 1
1078200, 5
2332016, 49
2362662, 2
2308436, 1
1885343, 2
2285968, 1
2211074, 24
2331989, 38
2321755, 6
1827359, 6
2117211, 6
1885324, 1
2116779, 6
1833803, 2
1833876, 2
2328356, 6
1577599, 6
1658211, 1
2112704, 21
1327627, 1
2081363, 2
1853935, 2
2117373, 6

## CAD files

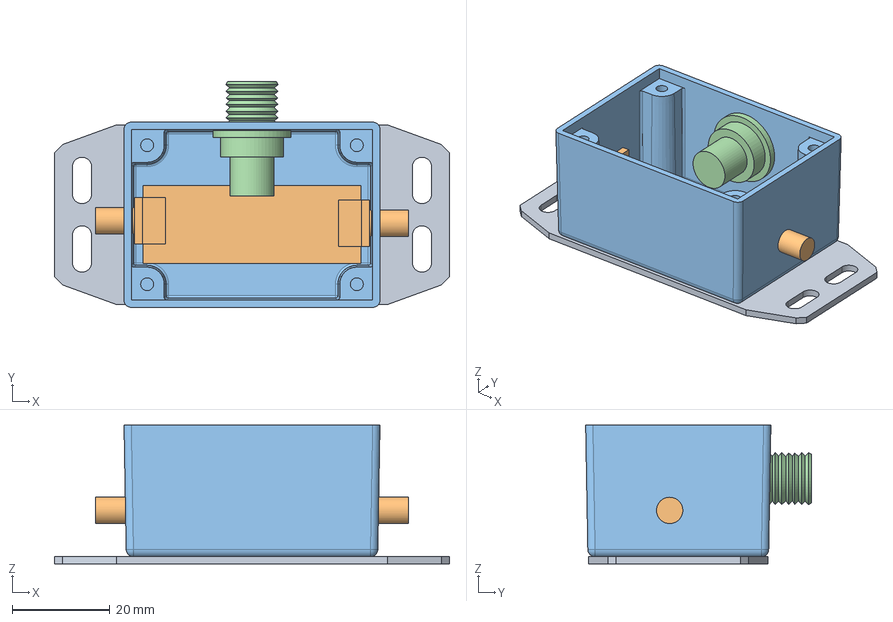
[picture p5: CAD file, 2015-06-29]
m2pa/model/assy.fcstd
81.0 x 46.3 x 28.5 mm
_590hf
_590hf001
power2

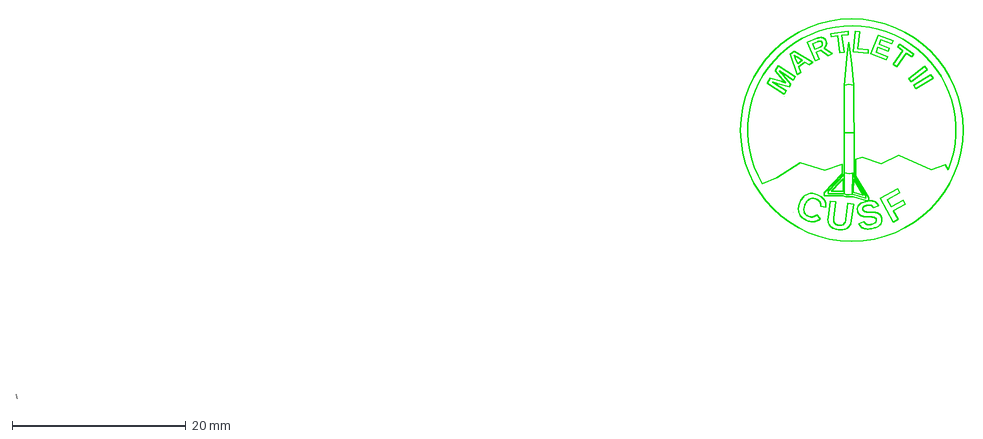
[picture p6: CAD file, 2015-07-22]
docs/emblem_path.dxf
109.5 x 44.0 mm

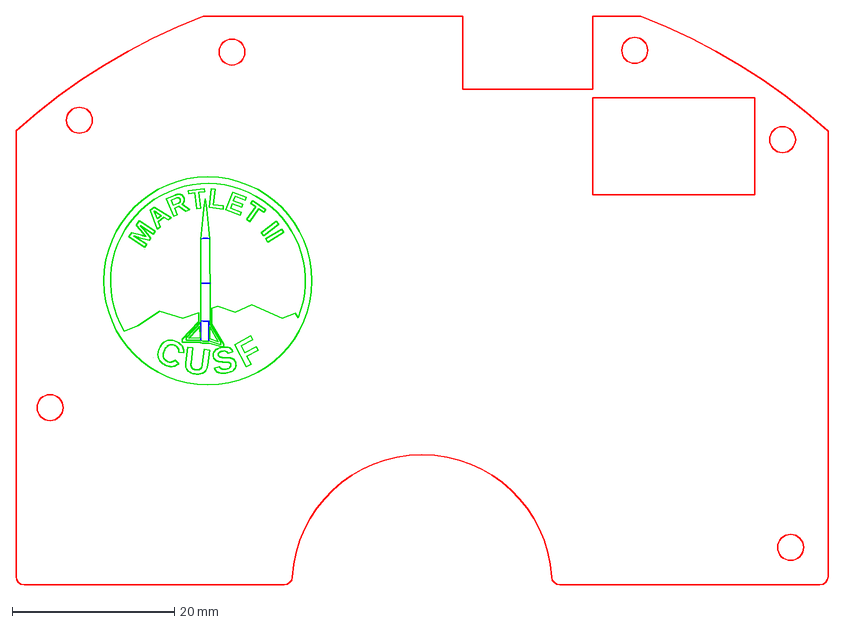
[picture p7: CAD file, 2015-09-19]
m2fc/pcb/cover/m2fc.dxf
100.0 x 70.0 mm

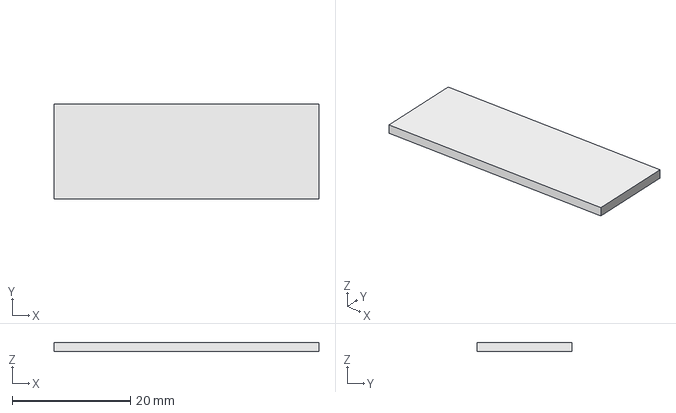
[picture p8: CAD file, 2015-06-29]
m2pa/model/m2pa.stp
44.8 x 16.0 x 1.60 mm

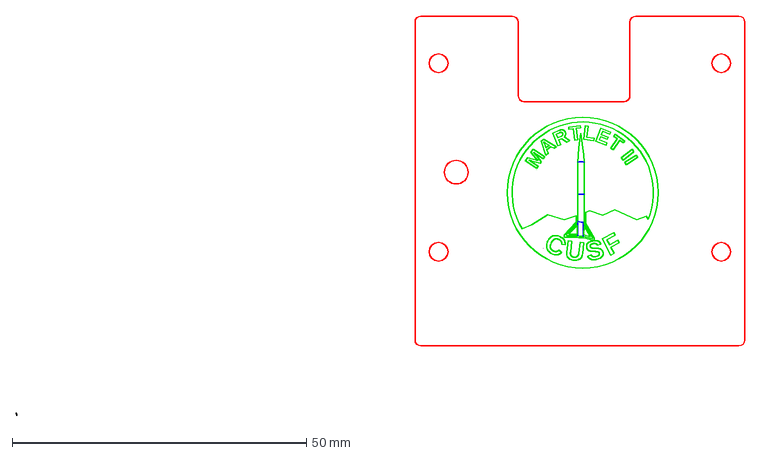
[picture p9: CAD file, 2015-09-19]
m2r/pcb_r2/cover/m2r-r2.dxf
123.7 x 67.9 mm

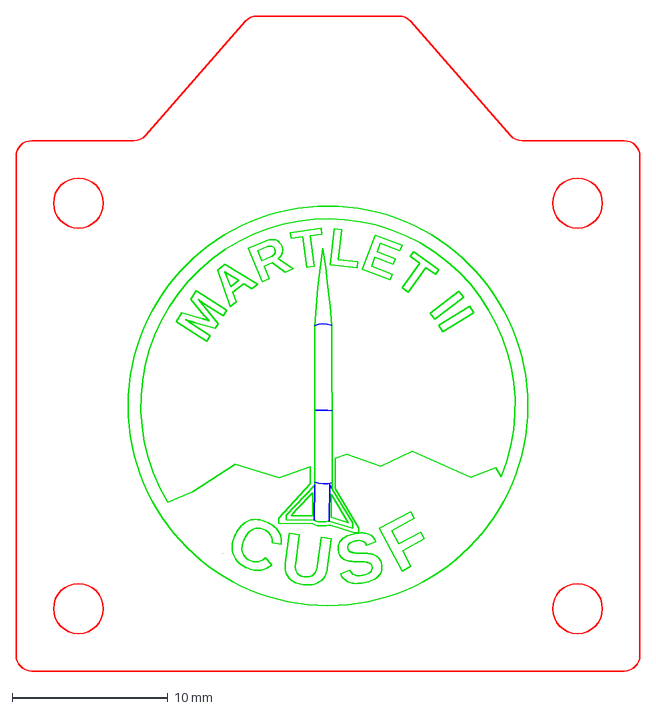
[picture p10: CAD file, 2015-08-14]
m2rl/pcb/cover/m2rl.dxf
40.0 x 42.0 mm

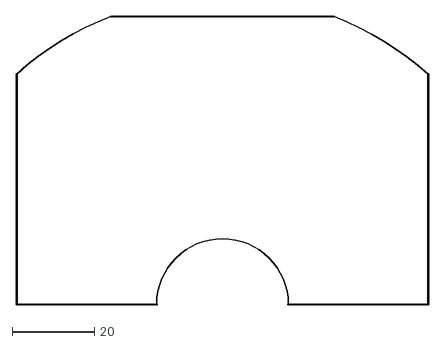
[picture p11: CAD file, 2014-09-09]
m2fc/pcb/outline/m2fc-Edge_Cuts.dxf
100.2 x 70.2

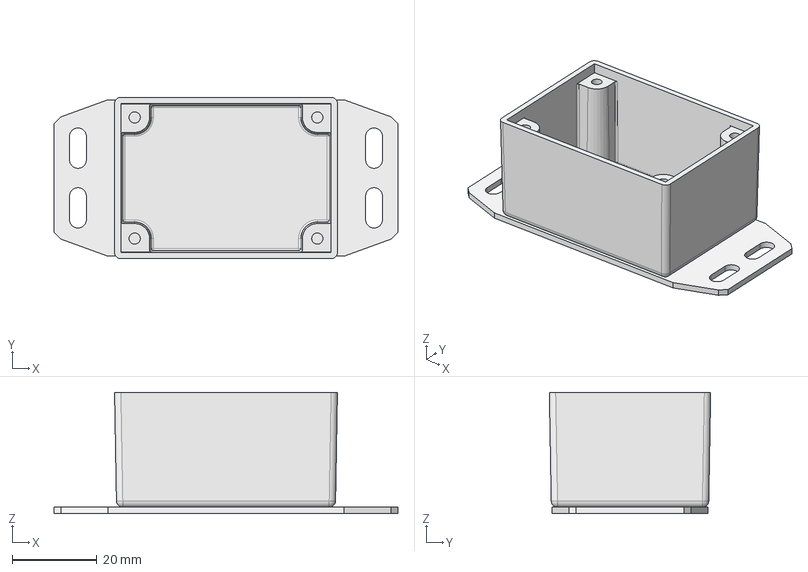
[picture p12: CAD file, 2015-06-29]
m2pa/model/1590hf.stp
81.0 x 38.0 x 28.5 mm

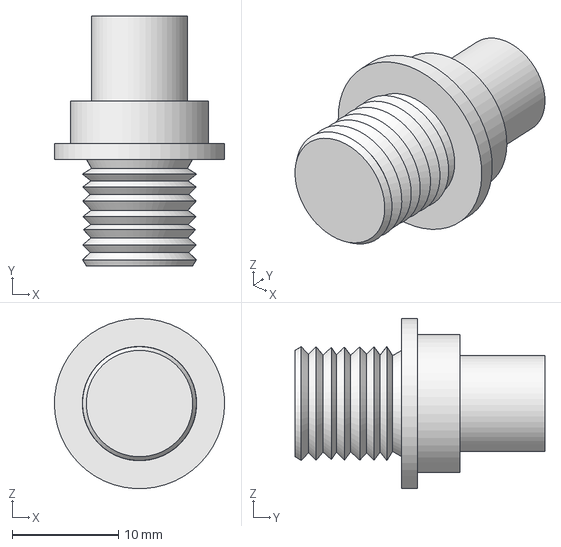
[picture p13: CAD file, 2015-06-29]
m2pa/model/power2.stp
16.0 x 23.5 x 16.0 mm

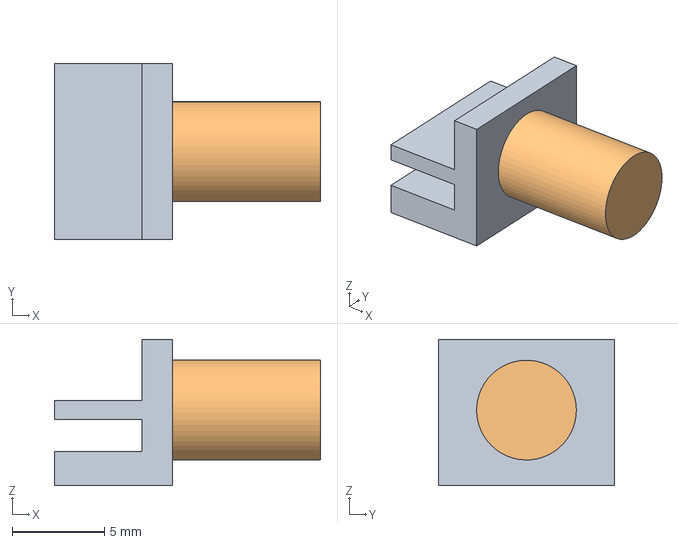
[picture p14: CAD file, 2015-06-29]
m2pa/model/sma.stp
14.4 x 9.52 x 7.92 mm

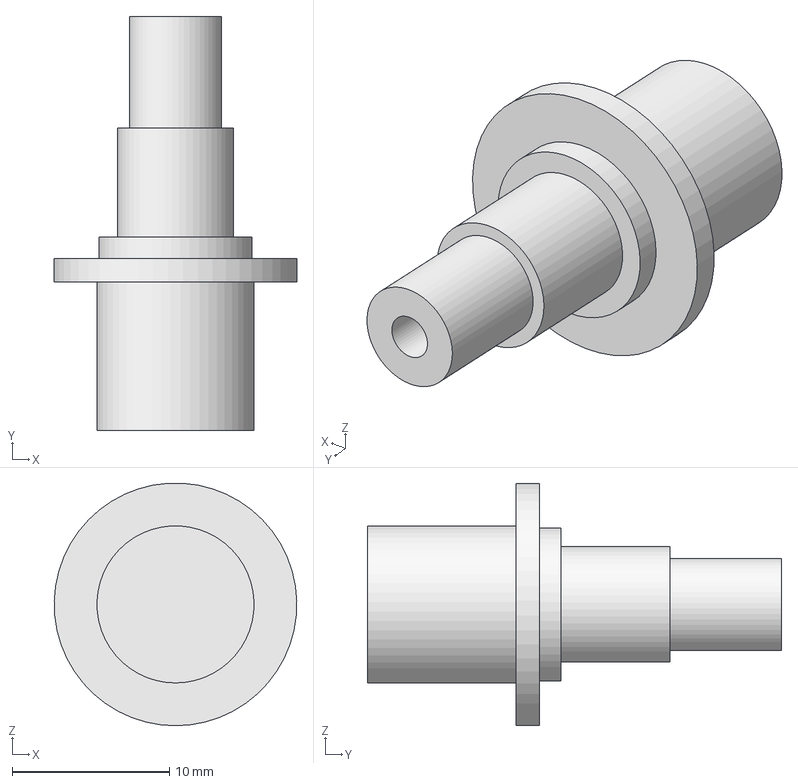
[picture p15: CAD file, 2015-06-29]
m2pa/model/power.stp
15.4 x 26.4 x 15.4 mm

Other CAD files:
m2fc/pcb/outline/m2fc-NPTH-drl_map.dxf
m2r/pcb/drawing/m2r-NPTH-drl_map.dxf
m2r/pcb/drawing/m2r-drl_map.dxf
m2fc/pcb/outline/m2fc-drl_map.dxf
m2pa/m2pa-tiny-F_Paste.dxf
m2pa/model/1590hf.fcstd
m2pa/model/m2pa.fcstd
m2pa/model/power.fcstd
m2pa/model/power2.fcstd
m2pa/model/sma.fcstd
m2r/pcb_r2/m2r-F_Paste.dxf
m2rl/pcb/m2rl-F_Paste.dxf

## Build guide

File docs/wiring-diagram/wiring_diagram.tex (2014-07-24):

\documentclass[a4paper]{article}
\usepackage{tikz}
\usetikzlibrary{positioning,calc}
\begin{document}
\pagestyle{empty}
\begin{tikzpicture}
    [scale=0.8,
     master/.style={draw=blue!100,thick,anchor=south,font=\LARGE},
     slave/.style={draw=blue!50,anchor=south,font=\large}]
    % Body
    \draw [double] (0, 0) -- (0, 15) -- (5, 25) -- (10, 15) -- (10, 0) -- (0, 0);

    % Fins
    \draw (0, 0) -- (-3, 0) -- (0, 5);
    \draw (10, 0) -- (13, 0) -- (10, 5);

    % Mounting Plates
    \draw [thick,double] (0, 7) -- (10, 7);
    \draw [thick,double] (0, 13.8) -- (10, 13.8);
    \draw [thick] (0, 15) -- (10, 15);
    \draw [thick] (1, 17) -- (9, 17);
    \draw [thick] (3, 21) -- (7, 21);

    % Main Body
    \node (fc1) at (5, 7) [master] {FC1};
    \node (fc1bat) [right=1 of fc1.south east] [slave] {Battery};
    \node (fc1arm) at (10, 7) [slave, anchor=south east] {Arming};
    \node (fc1led) [above=0 of fc1arm.north east] [slave, anchor=south east] {LED};
    \node (fc1pyro) [left=1 of fc1.south west] [slave] {Pyro};
    \node (fc1sg) at (0, 2) [slave, anchor=south west] {Strain Gauge$\times3$};
    \node (fc1tc1) [above=0 of fc1sg.north west] [slave, anchor=south west] {Thermocouple};
    \node (fc1tc2) at (0, 5) [slave, anchor=south west] {Thermocouple};
    \node (bcam) at (0, 7) [slave,anchor=south west] {Camera};

    \draw (fc1.190) |- (fc1pyro);
    \draw (fc1.110) |- (fc1led.165);
    \draw (fc1.100) |- ($(fc1arm.north west) + (0.2, 0.4)$) -- (fc1arm.154);
    \draw (fc1.90)  |- ($(fc1bat.north) + (0, 0.3)$) -- (fc1bat);
    \draw (fc1.230) |- (fc1tc2);
    \draw (fc1.250) |- (fc1tc1);
    \draw (fc1.270) |- (fc1sg);

    % Nosecone Base
    \node (fc2) at (4, 15) [master] {FC2};
    \node (fc2bat) [right=1 of fc2.south east] [slave] {Battery};
    \node (fc2arm) at (9, 15) [slave, anchor=south east] {Arming};
    \node (fc2led) [above=0 of fc2arm.north east] [slave, anchor=south east] {LED};
    \node (fc2pyro1) at (1, 15) [slave, anchor=north] {Pyro};
    \node (fc2pyro2) at (5, 15) [slave, anchor=north] {Pyro};
    \node (fc2pyro3) at (9, 15) [slave, anchor=north] {Pyro};

    \node (r) at (4.5, 17) [master] {Radio};
    \node (rbat) [right=1.1 of r.south east] [slave] {Battery};
    \node (rarm) [above=0 of rbat.north] [slave] {Arming};
    \node (rled) [above=0 of rarm.north] [slave] {LED};
    \node (rant) at (5, 21) [slave,anchor=north] {Antenna};
    \node (rb) [left=0.1 of r.south west] [slave,anchor=south east,align=center]
    {Satellite\\Modem};

    \node (ncam) at (5, 21) [slave,anchor=south] {Camera};
    \node (ntc) at (5, 25) [slave,anchor=south] {Thermocouple};

    \draw (fc2.250) |- (fc2pyro1);
    \draw (fc2.270) |- ($(fc2pyro3.south) - (0, 0.2)$) -- (fc2pyro3.south);
    \draw (fc2.290) |- ($(fc2pyro2.south) - (0, 0.1)$) -- (fc2pyro2.south);

    \draw (fc2.110) |- ($(fc2led.north west) - (0, 0.1)$);
    \draw (fc2.90)  |- ($(fc2arm.north west) + (0.3, 0.4)$) -- (fc2arm.151);
    \draw (fc2.70)  |- ($(fc2bat.north) + (0, 0.2)$) -- (fc2bat.north);
    \draw (fc2.130) |- (r.south);
    \draw (fc2.180) -| ($(ntc.west) - (4, 0)$) -- (ntc.west);

    \draw (r.east) |- (rbat.west);
    \draw (r.70) |- (rarm.west);
    \draw (r.110) |- (rled.west);
    \draw (r.130) |- (rant.200);
    \draw (r.west) |- (rb.east);
\end{tikzpicture}
\end{document}

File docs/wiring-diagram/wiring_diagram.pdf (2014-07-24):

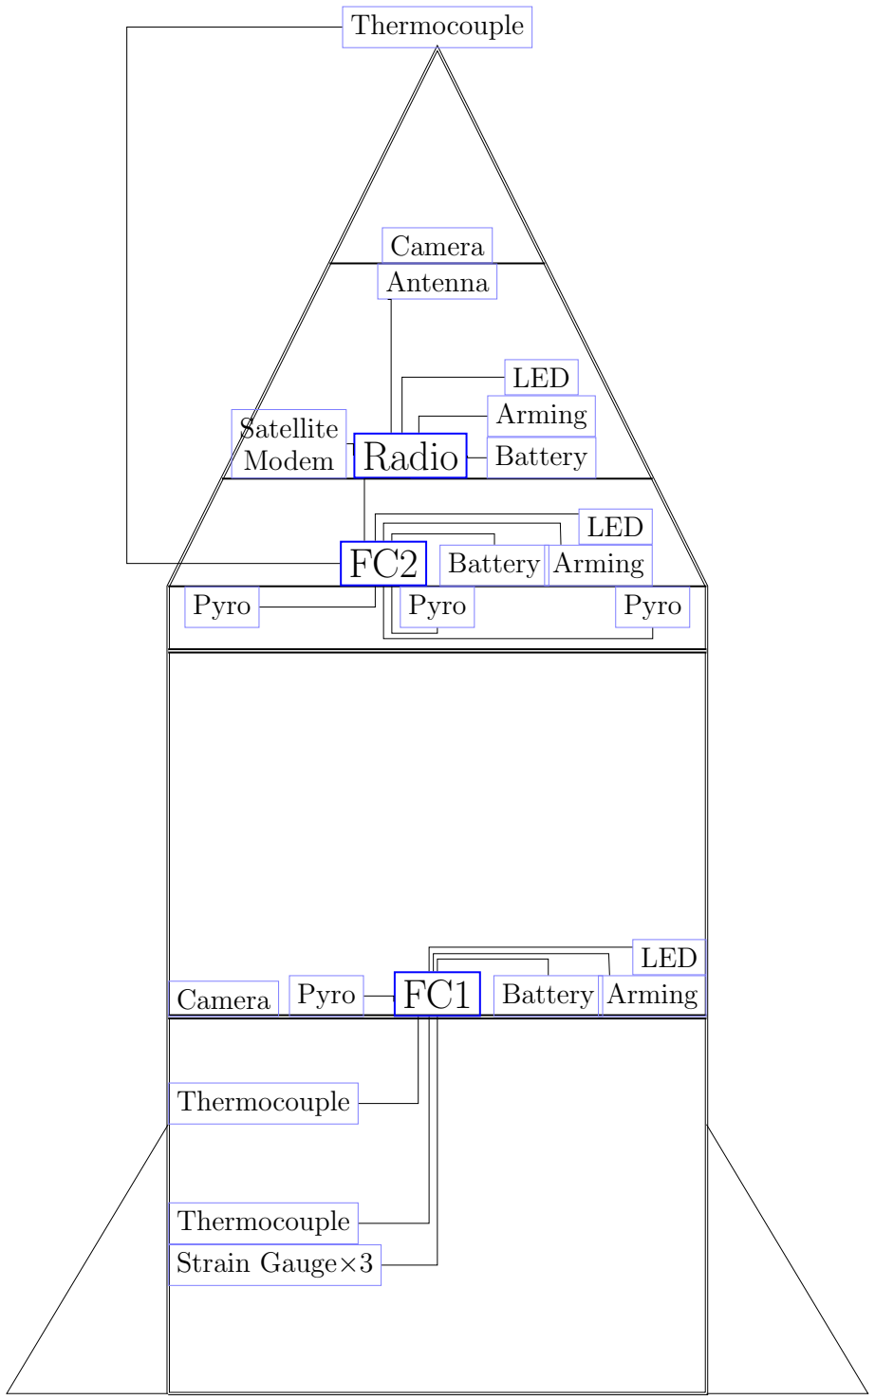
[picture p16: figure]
Battery; Arming; LED; Pyro; Strain Gauge×3; Thermocouple; Camera; Radio; Antenna; Satellite Modem

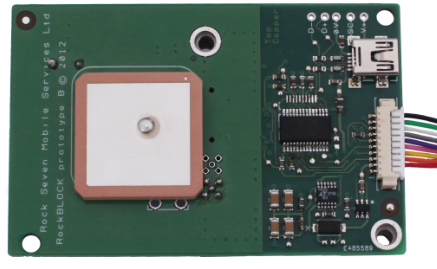
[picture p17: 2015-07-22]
docs/nosecone-wiring/rockblock.png

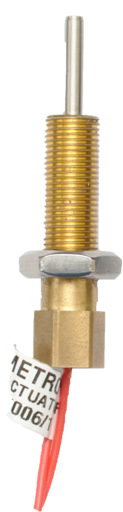
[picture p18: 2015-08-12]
docs/wiring-diagram/metron.png

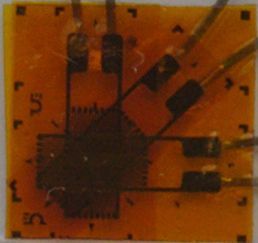
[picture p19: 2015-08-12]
docs/wiring-diagram/strain.jpg

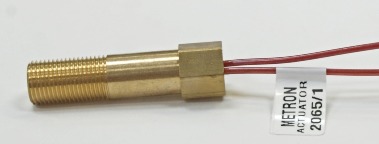
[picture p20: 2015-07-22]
docs/nosecone-wiring/metron.jpg

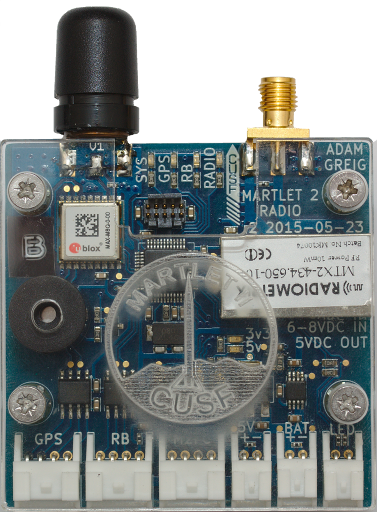
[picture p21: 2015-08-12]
docs/wiring-diagram/m2r.png

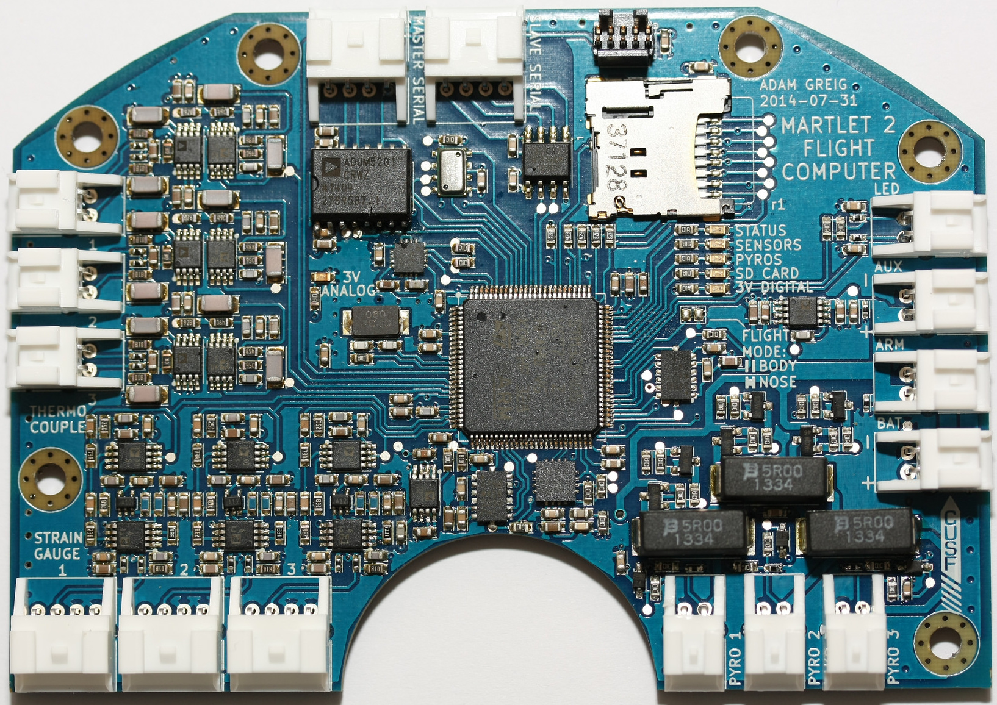
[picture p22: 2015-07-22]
docs/nosecone-wiring/m2fc.jpg

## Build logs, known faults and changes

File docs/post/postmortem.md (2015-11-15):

---
title: Martlet II Avionics Postmortem
author: Adam Greig, CU Spaceflight
date: October 2015

header-includes:
    - \usepackage{framed,color}
    - \definecolor{shadecolor}{rgb}{0.639,0.757,0.678}
    - \usepackage{fancyhdr}
    - \pagestyle{fancy}
    - \fancyhead[L]{}
    - \fancyhead[C]{Martlet II Avionics Postmortem}
    - \fancyhead[R]{\thepage}
    - \fancyfoot[R]{}
    - \fancyfoot[C]{}
---

\fancypagestyle{plain}{
\renewcommand{\headrulewidth}{0pt}
\fancyhf{}
\fancyhead[L]{\includegraphics[width=3cm]{cusf_logo}}
\fancyhead[R]{\includegraphics[width=3cm]{m2_logo}}
\setlength\headheight{50pt}
}
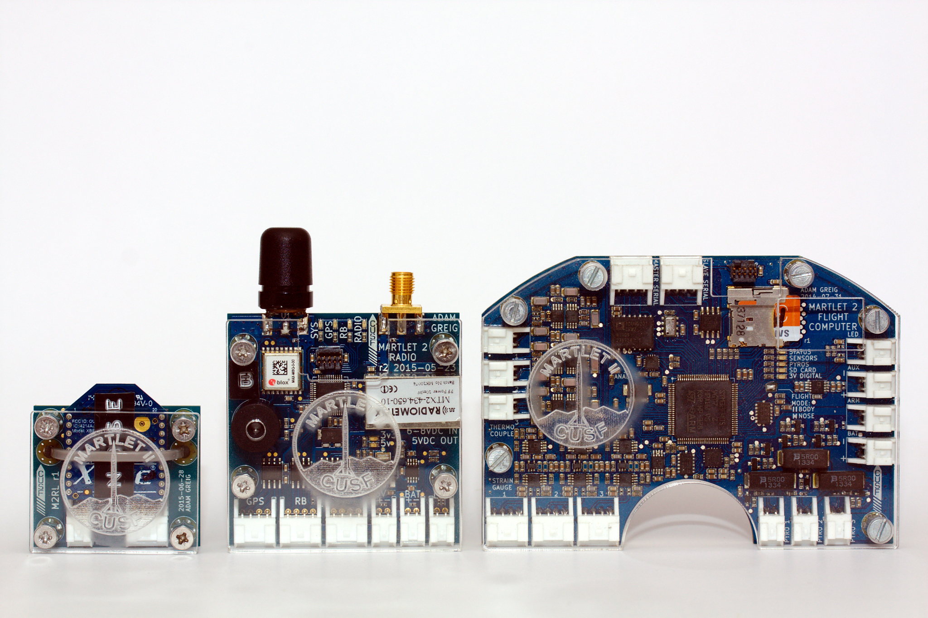
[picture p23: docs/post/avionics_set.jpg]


\clearpage

\setcounter{page}{1}

# Summary

## Overview

## Successes

## Problems

## Takeaways

\clearpage

\tableofcontents

# Introduction

## Martlet II Overview

Martlet 2 was an amateur rocket designed, built, and launched by Cambridge 
University Spaceflight in 2013-2015. It was intended to reach a speed of around 
1km/s and an altitude of around 15km, which would represent a new UK amateur 
record.

After a scrubbed launch due to weather in October 2014, Martlet 2 was launched 
in October 2015 from Black Rock Desert, Nevada, USA. An anomaly occurred three 
seconds into the flight, resulting in the rapid and thorough destruction of the 
rocket including the avionics. At this point the rocket is estimated to have 
reached an altitude of approximately 2km above ground level, and a velocity of 
approximately 1km/s. Much of the rocket structure and pieces of the avionics 
were recovered from the launch site.

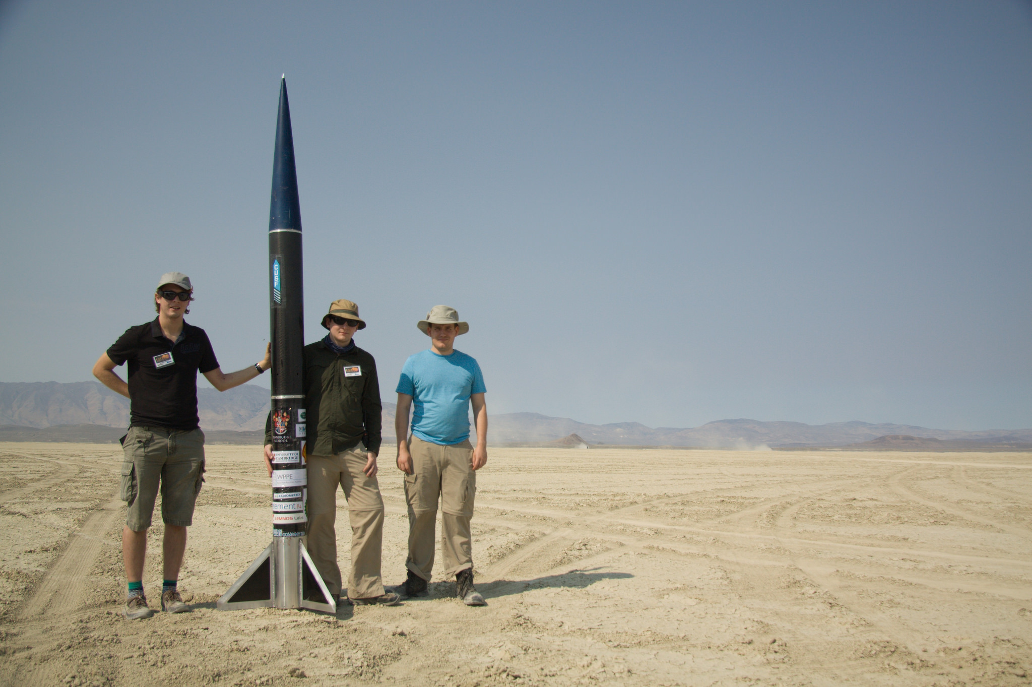
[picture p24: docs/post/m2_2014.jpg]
Martlet 2 in Black Rock Desert, Nevada, in October 2014


## Report Scope and Goals

A custom set of avionics was designed for Martlet 2. After the scrubbed launch, 
some were updated to address issues in the original designs. This document is a 
postmortem and a retrospective of those avionics, reviewing the original design 
and evaluating the choices made and lessons learnt for future avionics 
programmes.

This postmortem is concerned with the avionics and their integration with the 
larger rocket system, but will not discuss matters solely related to the rocket 
or other components, nor will it detail the flight anomaly except insofar as it 
relates to the avionics design and possibility for future improvements.

## Project Objectives

The original objectives for the avionics were, in priority order:

1. Control the recovery system deployment
1. Downlink rocket position information for recovery purposes
1. Record vital rocket parameters (altitude, velocity, acceleration, location)
1. Record additional sensors, including inertial, strain, and temperature
1. Downlink additional sensor readings and rocket state information

\begin{shaded}
Think carefully about precise objectives and priority. Lots of time was wasted 
on work that was not mission critical to the detriment of things that were.
\end{shaded}

# Avionics Overview

This section describes the hardware as-flown to give context to the rest of the 
postmortem.

## Custom Hardware

### M2FC

`M2FC` is the main flight computer. Onboard is an `STM32F405VGT6` 
microcontroller, a 32-bit, high performance ARM device. There is a MicroSD 
card; an inertial measurement unit (IMU) consisting of a low-G accelerometer 
(`ADXL345`), high-G accelerometer (`ADXL375`), gyroscope (`L3G4200D`), 
magnetometer (`HMC5883L`), and barometer (`MS5611`); three pyrotechnic 
channels; three strain gauge analogue inputs; three thermocouple analogue 
inputs; and two isolated serial ports. Additionally there are connectors for 
the main power supply battery, an arming switch (which is simply placed inline 
with the battery before power is provided to the board), an auxiliary power 
output, and a bicolour status LED.

There are two `M2FC`s, one in the nosecone and one on the body tube mounting 
plate.

### M2R

`M2R` is the radio board. Onboard is an `STM32F303CBT7` microcontroller, a 
uBlox `MAX-M8Q` GPS receiver, a Radiometrix `MTX2` FM radio transmitter, and a 
buzzer. There are connectors for power input, a status LED, two isolated serial 
ports (which attach to `M2FC` and the RockBLOCK satellite modem), and isolated 
access to the GPSs' serial port.

There is one `M2R`, in the nosecone of the rocket.

### M2RL

`M2RL` is a radio link between the two `M2FCs`. It consists of a series 2 Xbee 
modem and serial isolating hardware.

### M2PA

`M2PA` is a radio power amplifier, boosting the 10mW from `M2R` to around 500mW 
for transmission.

### JOEY

`JOEY` is a radio tracker designed for high altitude ballooning use. It has an 
onboard radio and GPS receiver and simply transmits the current GPS location. 
One `JOEY` board was installed in the parachute shroud as a backup locator.

## Other Electronics

Additionally there are two small cameras, a RockBLOCK satellite modem, two 
arming switches, three battery boxes, and four Metron protractors.

Installed in the fin are three strain gauges in a half-bridge configuration, 
with an unloaded set of strain gauges to provide temperature compensation, and 
a thermocouple to measure the fin root temperature.

### RockBLOCK

RockBLOCKs are Iridium satellite modems, capable of sending and receiving short 
messages anywhere in the world. One RockBLOCK was installed as a backup 
communication method in case the main radio link failed.

### PerfectFlite

A PerfectFlite commercial altimeter was installed on the body tube mounting 
plate to record the maximum altitude reached for official record-keeping 
purposes.

### Cameras

Two "808" miniature video cameras were installed, one in the nosecone looking 
downwards and one on the body tube mounting plate looking out into a 
downwards-facing mirror.

## Other Components

### Metrons

Metron protractors are pyrotechnic devices which, upon activation, displace a 
metal pin with significant force. Three are used to physically push the 
nosecone away from the rocket body, which causes the drogue parachute to be 
released, while one is used on the body tube mounting plate to release the main 
parachute.

TODO: Metron model

### Strain Gauges

Two units of a three-gauge rosette were mounted in one fin root, aligned with 
the flight axis, 45 degrees to the axis, and 90 degrees to the axis. The second 
unit was unloaded to provide temperature compensation.

TODO: Strain gauge model

### Thermocouples

A K-type thermocouple was installed in the fin root to record its temperature 
and that of the adjacent strain gauges.

### Battery Cases

4x AA battery boxes with PP3-style clips were used to store the flight 
batteries. Two of these were installed in the nosecone and one on the body tube 
mounting plate.

### Arming Switches

Keyed arming switches were used to control power to the avionics, with one in 
the nosecone and one on the body tube.

### Status LEDs

Bicolour status LEDs were used to indicate flight computer status. At launch, 
only one was fitted, on the body tube, connected to the body tube `M2FC`.

### Antenna

For the main radio downlink, a 434MHz folded bazooka dipole antenna was fitted 
in the upper section of the nosecone, secured to a nylon rod which ran through 
the nosecone avionics mounting.

## Interconnections

In the body of Martlet 2 is one `M2FC` connected to: the fin strain gauges and 
thermocouples, the body `M2RL`, the Metron to release the main parachute, a 
single battery box, an arming switch, a status LED, and providing power via the 
auxiliary connector to one camera (and `M2RL`). These devices are all mounted 
on the body tube bulkhead plate.

Most of the avionics are in the nosecone, where `M2FC` is connected to `M2R`, 
the nosecone `M2RL`, three Metrons for separating the nosecone and two battery 
boxes in parallel (each 4xAA Lithium primary cells). Its auxiliary power 
connector provides power to two cameras, `M2RL` and `M2R`. `M2R` is connected 
to the RockBLOCK and `M2PA` which in turn is connected to the antenna. These 
devices were all mounted on an aluminium structure affixed to the base of the 
nosecone.

See the wiring diagram for a more detailed representation.

System Overview

# Project Management

## Time Management

## Collaboration

## Prioritisation and Feature Freeze

# System Review

Little thought was put into the whole system design early on, such as 
interlinking the avionics and regulating and distributing the power supply. 
Much of this had to be designed once the rest of the avionics were finalised, 
which led to a suboptimal solution.

\begin{shaded}Consider how individual components will form the complete system 
before finalising their design.\end{shaded}

# Hardware Review

This section will address the design, manufacture, and testing of the avionics.

## Technology Choices

All PCB design was performed in KiCAD. While a few issues were encountered due 
to version upgrades during the development programme, in general this software 
worked well.

Setting up a common library of component symbols and footprints from the 
beginning would probably have saved time over copying symbols separately for 
each each project.

\begin{shaded}Establish a common library for symbols and footprints which all 
projects can share.\end{shaded}

## Design Procedure

The current procedure for carefully checking schematic and board layout led to 
only a single mistake in production: the powered isolator `ADuM5201` was given 
a normal-width `SOIC16` footprint where the datasheet called for a wide 
variant. Luckily the chip was easily modified be folding the legs around so 
this did not present a serious issue in production.

\begin{shaded}Careful and thorough checking of the PCB designs, including 
against the CUSF checklist, resulted in very few issues on a complicated 
design.\end{shaded}

Manufacture was by reflow soldering and had no issues beyond a few small solder 
bridges which were readily reworked. Again standard procedures seem to have 
worked very well here.

## M2FC

The early design called for a pyrotechnic board `M2P` to control the recovery 
system and a datalogging board `M2D` to record flight data. The decision was 
made early on to combine the pyrotechnic board and the datalogging board into 
the flight computer `M2FC`, as they required some very similar sensors and 
software. In retrospect, it seems likely that keeping these separate would have 
been beneficial: the recovery system could be simpler and thus more reliable, 
and the datalogger could be worked in isolation allowing better development 
collaboration with less risk of compromising the main objectives.

\begin{shaded}
Consider maintaining modularity even when integration is tempting; it preserves 
isolation and separation of concerns.
\end{shaded}

### Analogue Section

`M2FC`'s analogue section is responsible for converting the small electrical 
signals from the thermocouples and strain gauges into useful levels at the ADC. 
The design used specialised amplifiers as a frontend followed by a dual active 
antialiasing filter. These parts ended up being a substantial fraction of the 
total avionics cost, but were high specification and performed as required 
during testing and during flight. Additional testing and characterisation would 
have been useful and more time could have been allocated to this. In future 
less potent antialiasing filters might be sufficient but this design appears to 
have worked well.

### Pyrotechnic Drivers

The pyrotechnic channels consisted of a small N-channel MOSFET driving the gate 
of a higher current P-channel MOSFET which controlled high side power to the 
Metron protractors. Each channel additionally had a high power 5$\Omega$ 
resistor in series to limit total current, and a continuity measurement 
circuit. The high power resistors are physically large devices and it unclear 
how crucial they are; additional testing or characterisation may be useful in 
future.

The channels were not tested with the actual Metron devices until it was far 
too late to remedy any defects, instead only being tested with other 
pyrotechnic devices. This was a serious testing defect. In the event, the DC 
current provided through the pyrotechnic channel was insufficient to fire a 
Metron, but luckily using 10ms duration pulses instead proved reliable. The 
datasheet for the Metron devices claims a lower all-fire current with such 
pulses, so this is to be expected. This lucky escape meant no hardware 
alterations had to be performed.

\begin{shaded}Test pyrotechnic drivers with the flight pyrotechnic 
devices.\end{shaded}

The continuity testing worked as designed. In future resistance measurement 
would provide more information and may be able to indicate faulty connections.

### Inertial Measurement Unit

The IMU consisted of a number of low-cost individual MEMS sensors. On the whole 
this design worked to within acceptable limits, with some issues.

The two accelerometers worked well and having the two acceleration ranges 
covered was helpful. The barometer worked very well but did not appear to 
indicate when a conversion was complete despite datasheet claims, so had to be 
polled instead, though this only caused a slightly lower data rate.

The gyroscope appeared somewhat unreliable and additionally is a more obtuse 
sensor than the accelerometer. Some fault likely lies in the additional 
complexity of I2C instead of SPI. In future attempting to stick to SPI devices 
would probably simplify matters.

The magnetometer had similar issues to the gyroscope. Neither were required for 
flight computer operation however, so this did not present issues in this 
flight. For flights requiring a higher degree of state estimation, it may be 
prudent to select alternative gyroscopes and magnetometers.

Fully and partially integrated IMU sensors are available which would reduce 
alignment errors and simplify communication and drivers.

\begin{shaded}Consider using a more integrated IMU solution, or at least keep 
everything on an SPI bus and choose a different magnetometer and 
gyroscope.\end{shaded}

### SD Card

Both `M2FC`s had an SD card to store flight logs. SD cards have the serious 
advantages of high storage density, high write speeds, low cost, ready 
availability, high survivability, and ease of connection to a computer. 
Interfacing to them was straightforward and allowed high rate data to be stored 
without concern for filling up the storage space.

Mechanically they presented some issues. Connectors tend to emphasise ease of 
insertion/removal which is undesirable in this application. There were concerns 
that high vibrations and accelerations would cause the SD cards to bounce on 
their contact pins or even eject from the holder. The only obvious remedy was 
to use adhesive to secure the SD card, which complicates reading data off them 
after the flight.

Alternatives were considered such as onboard flash memory or eMMC. Onboard 
flash can be soldered down, but tends to either come in very low storage space, 
or large packages with high pin count parallel interfaces. eMMC is even worse 
in this regard, with most packages difficult to solder and requiring more 
complicated interface circuitry.

In the event some issues were encountered with SD card retention; see below for 
details.

On balance the SD card seems the best solution for high rate data, but perhaps 
lower rate flash storage could be useful as a backup for critical data.

### Off-Board Integrations

## M2R

### Radio

### GPS

### RockBLOCK

### Buzzer

## M2RL

The original design to interconnect the two `M2FC` boards, in the nosecone and 
in the body tube, was to use pogo pins on an interface board mounted near the 
nosecone separation point. This design proved very fiddly and delicate, with 
the pogo pins repeatedly breaking off during assembly. A more robust connector 
would be required for this sort of interface.

After the 2014 scrub, `M2RL` was designed to provide a radio link between the 
boards instead. This was much easier to integrate with the rocket design. 
Unfortunately time constraints meant this was not active during the flight, so 
its potential performance is unknown.

In future such radio links could be integrated onto the flight computers or 
possibly just downlinked to the ground station directly.

## M2PA

Originally a power amplifier based on the `ADL5324` device was installed on 
`M2R` but being integrated made it difficult to test and tune. After the 
scrubbed launch the amplifier was moved to its own board, `M2PA`. This made 
testing easier but took substantially more payload space.

The amplifier design was fairly successful, meeting specification. In future 
this design could probably be used integrated. Alternative amplifiers have 
become available which require substantially fewer external tuning components 
and offer higher powers which might be superior, such as the Skyworks 
`SKY65116`.

After the 2014 scrub, the power amplifier was moved off `M2R` and into its own 
box. This design worked well and the amplifier survived the flight. It's 
possible that in future returning to an integrated amplifier once the design is 
proven would have worked well too, simplifying avionics wiring.

## JOEY

As a backup locating device, a Joey tracker was installed in Martlet 2 as well. 
It had its own independent power supply, GPS, and radio. While this was not 
required in the event, its presence was reassuring and there is no reason to 
believe it would not have worked (had it not been torn to pieces during 
flight).

\begin{shaded}Use a totally separate and independent tracker for 
backup.\end{shaded}

## Arming Concept

The design for arming the avionics system was essentially a power switch on the 
body of the rocket, which controlled all power to the avionics. Obviously with 
the switch off, no pyrotechnic devices could fire, ensuring the rocket was 
safe. Two power switches were required, on the nosecone and on the body tube.

The connection to the power switch was provided on `M2FC`, which connected 
directly to the battery pack and then placed the arming switch in series before 
drawing any power.

This design was fairly simple but several issues were encountered

## Power Management

The power distribution design was not considered until after the majority of 
the avionics were finalised. Each piece of avionics had been designed with the 
assumption that somehow around 6-7V of battery power would be available, as an 
appropriate voltage to regulate down to 5V and 3.3V for electronics systems 
while also providing enough margin to reliably fire the Metron protractors used 
in the recovery system. The design was therefore to use 4xAA lithium primary 
cells in a battery, connected to `M2FC`, which would then power the rest of the 
system once armed through the `AUX` connector.

In the original design, `M2R` had its own separate battery supply and thus 
arming/power switch. In the 2014 scrub update, `M2R` is instead powered on the 
`AUX` bus from `M2FC`, which uses both battery packs in parallel to give 
maximum capacity for the combined system. This new design allowed for a single 
power switch which reduced complexity.

\begin{shaded}Don't use separate batteries for otherwise interdependent and 
connected systems, it just increases complexity. Central power switching is 
nice.\end{shaded}

Using lithium primary cells had some advantages for mass, power density, 
availability, and transport. CU Spaceflight have successfully used these cells 
for many varied missions so they were an obvious choice here. Being able to 
install a known-fresh set of batteries immediately prior to flight was 
reassuring, and being able to purchase these batteries at most large shops 
worldwide was likewise useful.

However, they necessitate battery holders which were all either difficult to 
mount securely, awkwardly shaped, or both. Reliable connections to the cells 
under the high acceleration conditions expected in flight was a pressing 
concern. In the original design, large Bulgin holders were used, but they were 
very awkward to fit in the mounting design. Post-scrub, smaller regular holders 
were used, but they did not provide any mounting points and were essentially 
friction fitted into a smaller compartment. Neither design was ideal, although 
it appears that the eventual design did provide power during acceleration.

In future it would be well worth considering a lithium ion rechargable main 
system battery with a dedicated power distribution board that can monitor and 
provide power to system components individually. Voltages could be regulated to 
some extent centrally, and supply currents could be measured, providing useful 
debugging information. Recharging allows for shore power to be used via an 
umbilical, which means the rocket may be powered up and on the pad for long 
durations, reducing urgency once padded up.

\begin{shaded}Give more thought to power supply design and distribution, 
including the option of rechargable batteries and an umbilical providing shore 
power.\end{shaded}

## Other Electronics

Beyond `M2FC` and `M2R` there were several other electronics systems on Martlet 
2, some integrated with the main avionics.

### RockBLOCK

`M2R` connected to a RockBLOCK Iridium satellite modem, which could relay 
position information from anywhere in the world. While a nice backup, this was 
probably not necessary at the launch site (a complete flat) and added 
complication to the avionics design and mounting. In the event the satellite 
modem did not have a chance to send any messages. In theory it is quite 
functional and would be useful on a future project where this level of backup 
communication is required.

\begin{shaded}Satellite modems can work well but consider if it is really 
required for a given flight, compared to the mass, power, and complexity 
cost.\end{shaded}

### PerfectFlite

To ensure the altitude reached would be recognised for record keeping purposes, 
a commercial altimeter (a PerfectFlite model) was fitted. No issues were found 
with this totally isolated system, although again clearer design on mounting 
and integration would have simplified launch operations.

### Cameras

We originally fitted a GoPro Hero camera and a Mobius ActionCam, both activated 
manually (the GoPro over the radio) before launch. After the 2014 scrub, the 
camera plan was updated to use only "808 #16" cameras, configured to begin 
recording when power is applied. They were then connected to `M2FC`'s auxiliary 
power output, so they began recording when the rocket was armed. This system 
worked very well and made final arming easier. Unfortunately during the flight 
anomaly the cameras were broken up and the SD cards were lost.

\begin{shaded}Small 808 cameras worked well. Activating them via the main 
avionics was a good idea. In future, secure the SD cards as well as possible, 
perhaps by gluing.\end{shaded}

## Other Components

### Metrons

### Strain Gauges

* Assembly issues
* Potential to short out excitation, putting whole flight computer at risk

### Thermocouples

### Battery Cases

### Arming Switches

### Status LEDs

### Antenna

## Interconnects

* Spec55 is wonderful
* JST PA did a good job
* External connectors in future
* Connector in the airframe?
* Umbilical to shore?

## Manufacture

### Issues Encountered

## Testing

# Software Review

## Technology Choices

## Reliability Management

### Watchdogs

### Hardware Error Handling

## Calibration

* Accels calibrate offset obviously, need to rotate for scale

## Drivers

## Flight State Machine

### Safety Timeout

### Ignition Detection

## Status Collection and Reporting

## Telemetry Collection, Forwarding and Storage

## Software Interfaces

## Testing

## Ground Station Software

## Release Management

# Integration Review

## Mounting

* Don't glue things
    * Really Really Really
    * LED broke off
    * Arming switch broke off
    * Other arming switch broke off
    * Arming key broke off
    * Both cameras broke off eventually
    * Don't glue things

## Enclosures

* More enclosed
* Easier to assemble
* No need to open to reprogram etc

## Switches and LEDs

## Cameras

## Antennas

## Cabling

## Sensors

# Launch Retrospective

## Missing Features

## Assembly

## Performance

### Radio

### Datalogging

### Sensors

### State Estimation

### Pyrotechnics

### Flight State

## Issues Encountered

### No RockBLOCK Signal In Enclosure

### Accidental Metron Firing During Assembly

### Arming Switch Location

* Too high up
* Behind launch rail

### Radio Not Enabled

* Required reprogramming

### Arming Key Broke

### Arming Switch Detached

### Status LED Detachedo

### Upright Requirement

### Ignition Detection Sensitivity

### Lack of Safety Timeout

### Early Body Metron Firing

### SD Cards Lost

# Conclusions and Recommendations

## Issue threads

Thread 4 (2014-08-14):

M2R MTX2 test pins close to MTX2

adamgreig, 2014-08-14:
The test pads for the four MTX2 data lines are a little too close to the metal of the case.

adamgreig, 2015-07-16:
Fixed in r2.

Closed 2015-07-16.

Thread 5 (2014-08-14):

M2FC ADUM5201 footprint wrong

adamgreig, 2014-08-14:
Should be SOIC16W not SOIC16. To fix, bend all the legs around under the chip before soldering.

adamgreig, 2015-07-16:
Fixed in M2RL.

Closed 2015-07-16.

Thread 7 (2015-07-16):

Battery monitoring resistors too close on m2r-r2

adamgreig, 2015-07-16:

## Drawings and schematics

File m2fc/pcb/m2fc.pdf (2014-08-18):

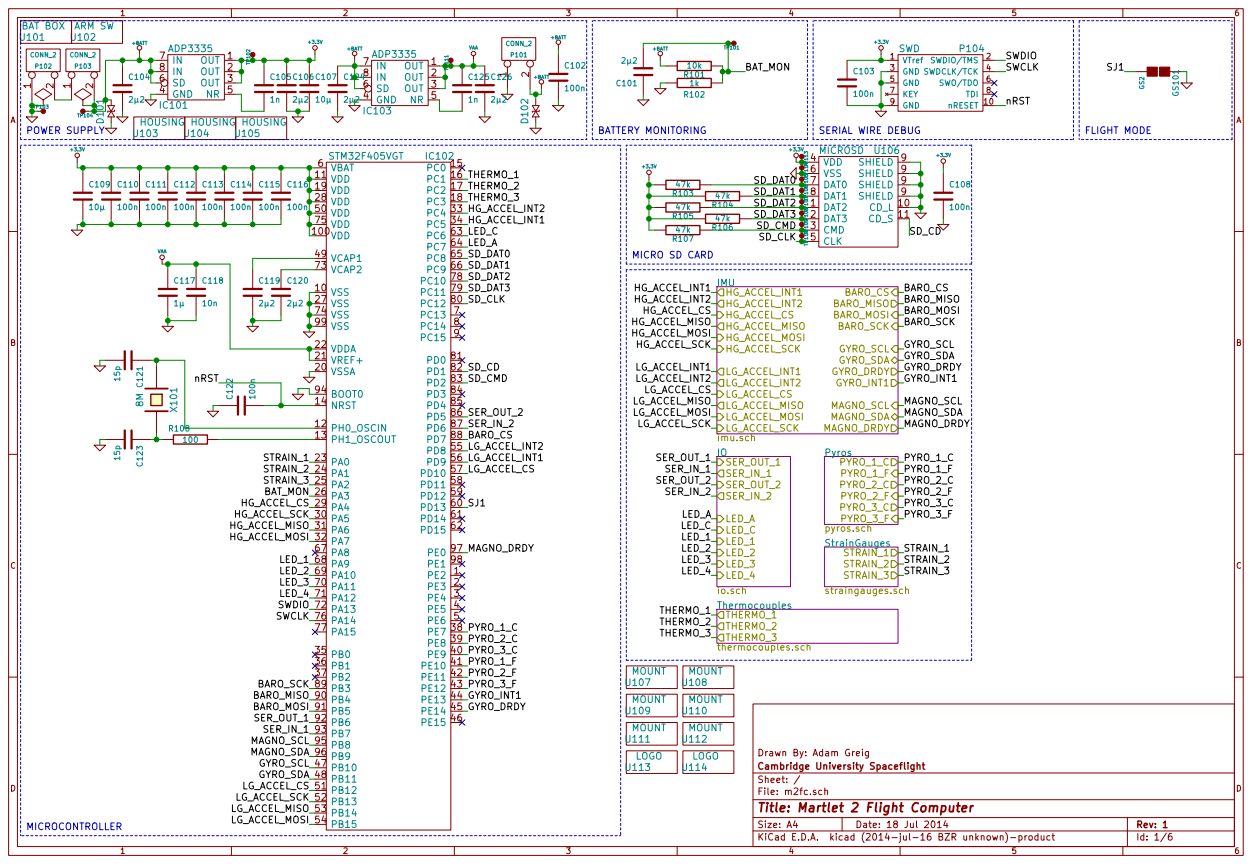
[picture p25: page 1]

Drawn By: Adam Greig
Id: 1/6 Title: Martlet 2 Flight Computer File: m2fc.sch Sheet: / Cambridge University Spaceflight

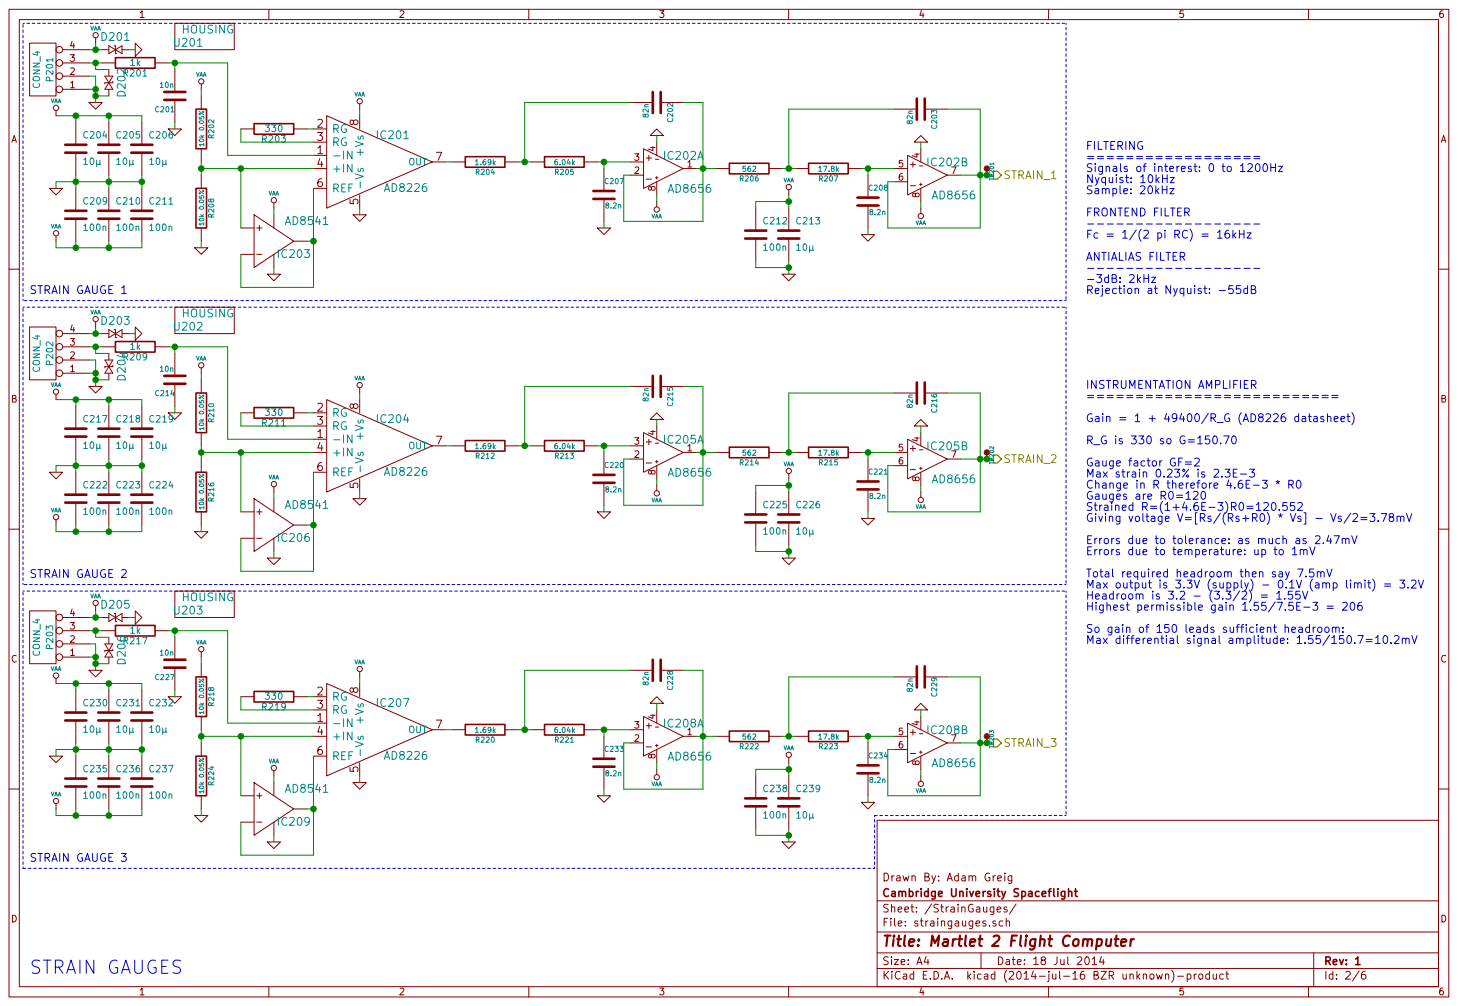
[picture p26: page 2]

FILTERING
================== Signals of interest: 0 to 1200Hz
Nyquist: 10kHz
Sample: 20kHz
FRONTEND FILTER
------------------ Fc = 1/(2 pi RC) = 16kHz

Gauge factor GF=2 Max strain 0.23% is 2.3E-3 Change in R therefore 4.6E-3 * R0

Gauges are R0=120
Strained R=(1+4.6E-3)R0=120.552
Giving voltage V=[Rs/(Rs+R0) * Vs] - Vs/2=3.78mV
Errors due to tolerance: as much as 2.47mV
Errors due to temperature: up to 1mV
Total required headroom then say 7.5mV
Max output is 3.3V (supply) - 0.1V (amp limit) = 3.2V
Headroom is 3.2 - (3.3/2) = 1.55V
Highest permissible gain 1.55/7.5E-3 = 206
So gain of 150 leads sufficient headroom:
Max differential signal amplitude: 1.55/150.7=10.2mV

Drawn By: Adam Greig
Cambridge University Spaceflight
Sheet: /StrainGauges/
File: straingauges.sch
Id: 2/6 Title: Martlet 2 Flight Computer

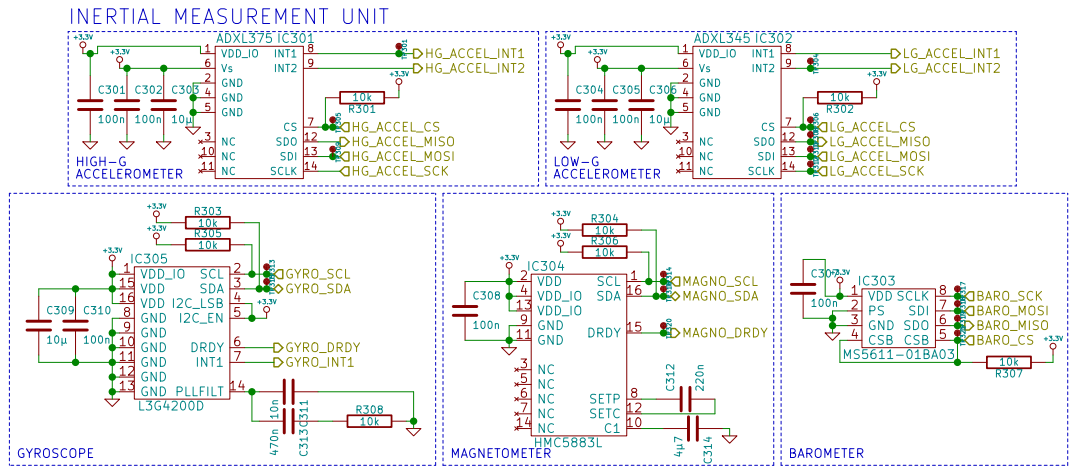
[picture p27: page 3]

Drawn By: Adam Greig
Id: 3/6 Title: Martlet 2 Flight Computer File: imu.sch Sheet: /IMU/ Cambridge University Spaceflight

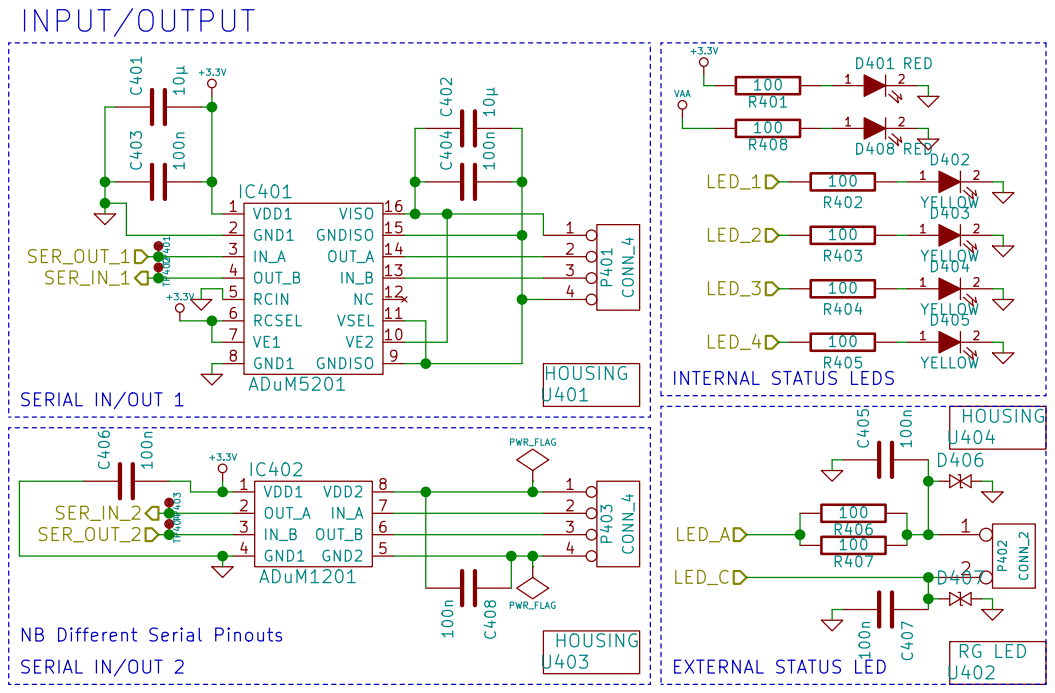
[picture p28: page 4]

NB Different Serial Pinouts
SERIAL IN/OUT 2

Drawn By: Adam Greig
Id: 4/6 Title: Martlet 2 Flight Computer File: io.sch Sheet: /IO/ Cambridge University Spaceflight

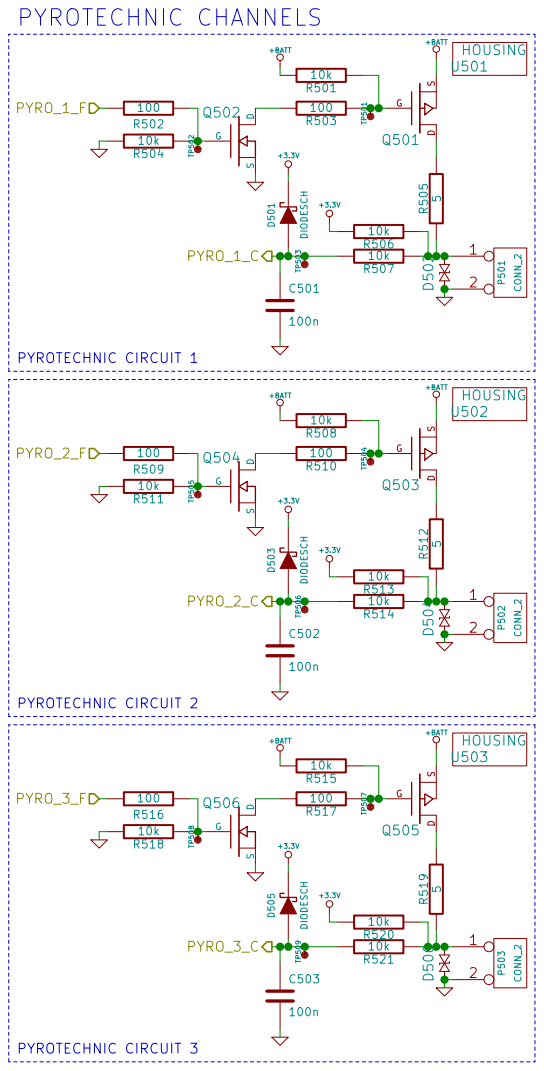
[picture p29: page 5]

Drawn By: Adam Greig
Cambridge University Spaceflight
Sheet: /Pyros/
File: pyros.sch
Id: 5/6 Title: Martlet 2 Flight Computer

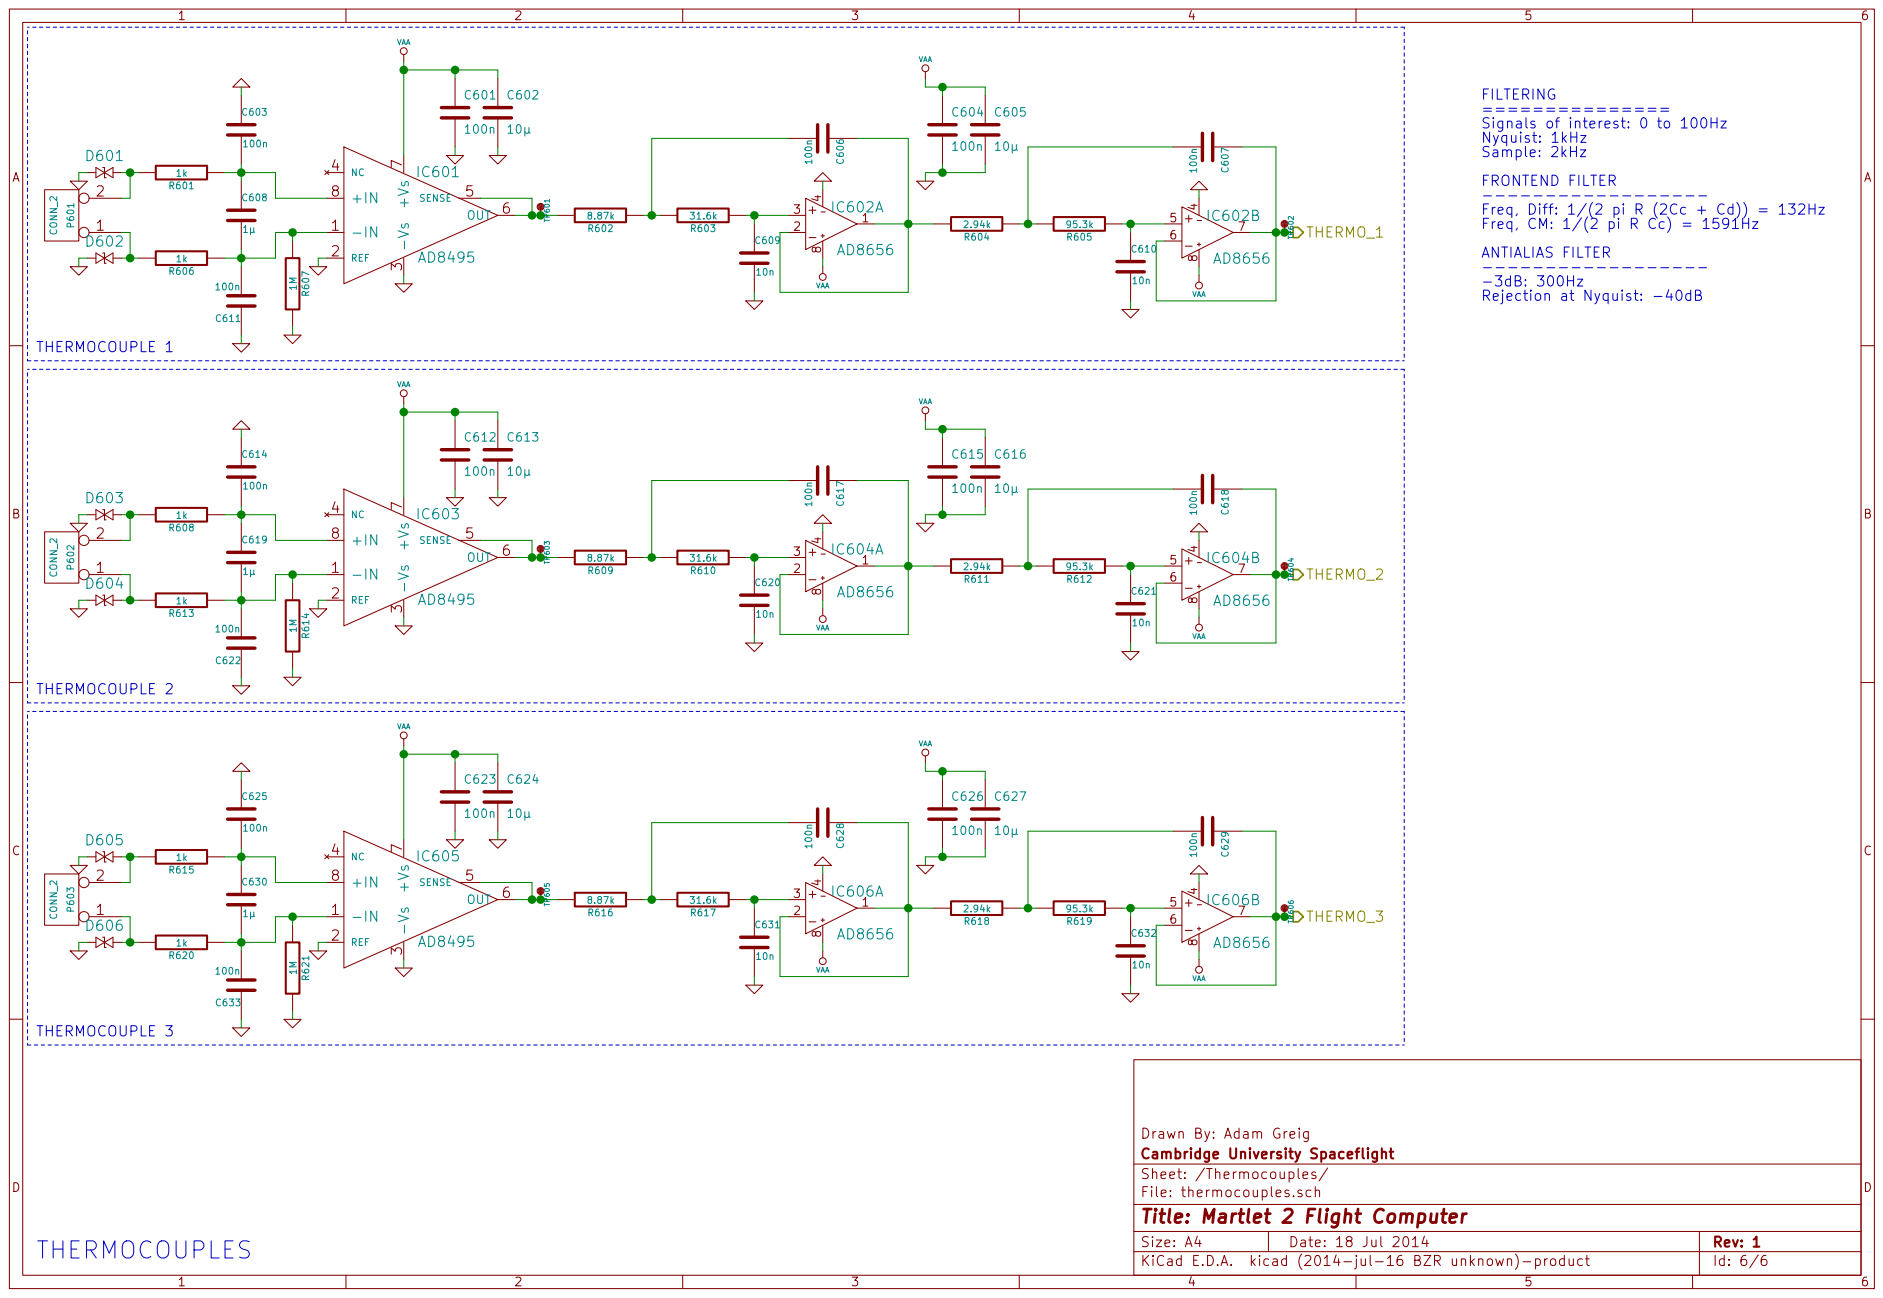
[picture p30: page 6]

FILTERING
=============== Signals of interest: 0 to 100Hz
Nyquist: 1kHz
Sample: 2kHz
FRONTEND FILTER
------------------ Freq, Diff: 1/(2 pi R (2Cc + Cd)) = 132Hz
Freq, CM: 1/(2 pi R Cc) = 1591Hz
ANTIALIAS FILTER
-3dB: 300Hz Rejection at Nyquist: -40dB

Drawn By: Adam Greig R607 1M

Cambridge University Spaceflight
Sheet: /Thermocouples/
File: thermocouples.sch
Id: 6/6 Title: Martlet 2 Flight Computer

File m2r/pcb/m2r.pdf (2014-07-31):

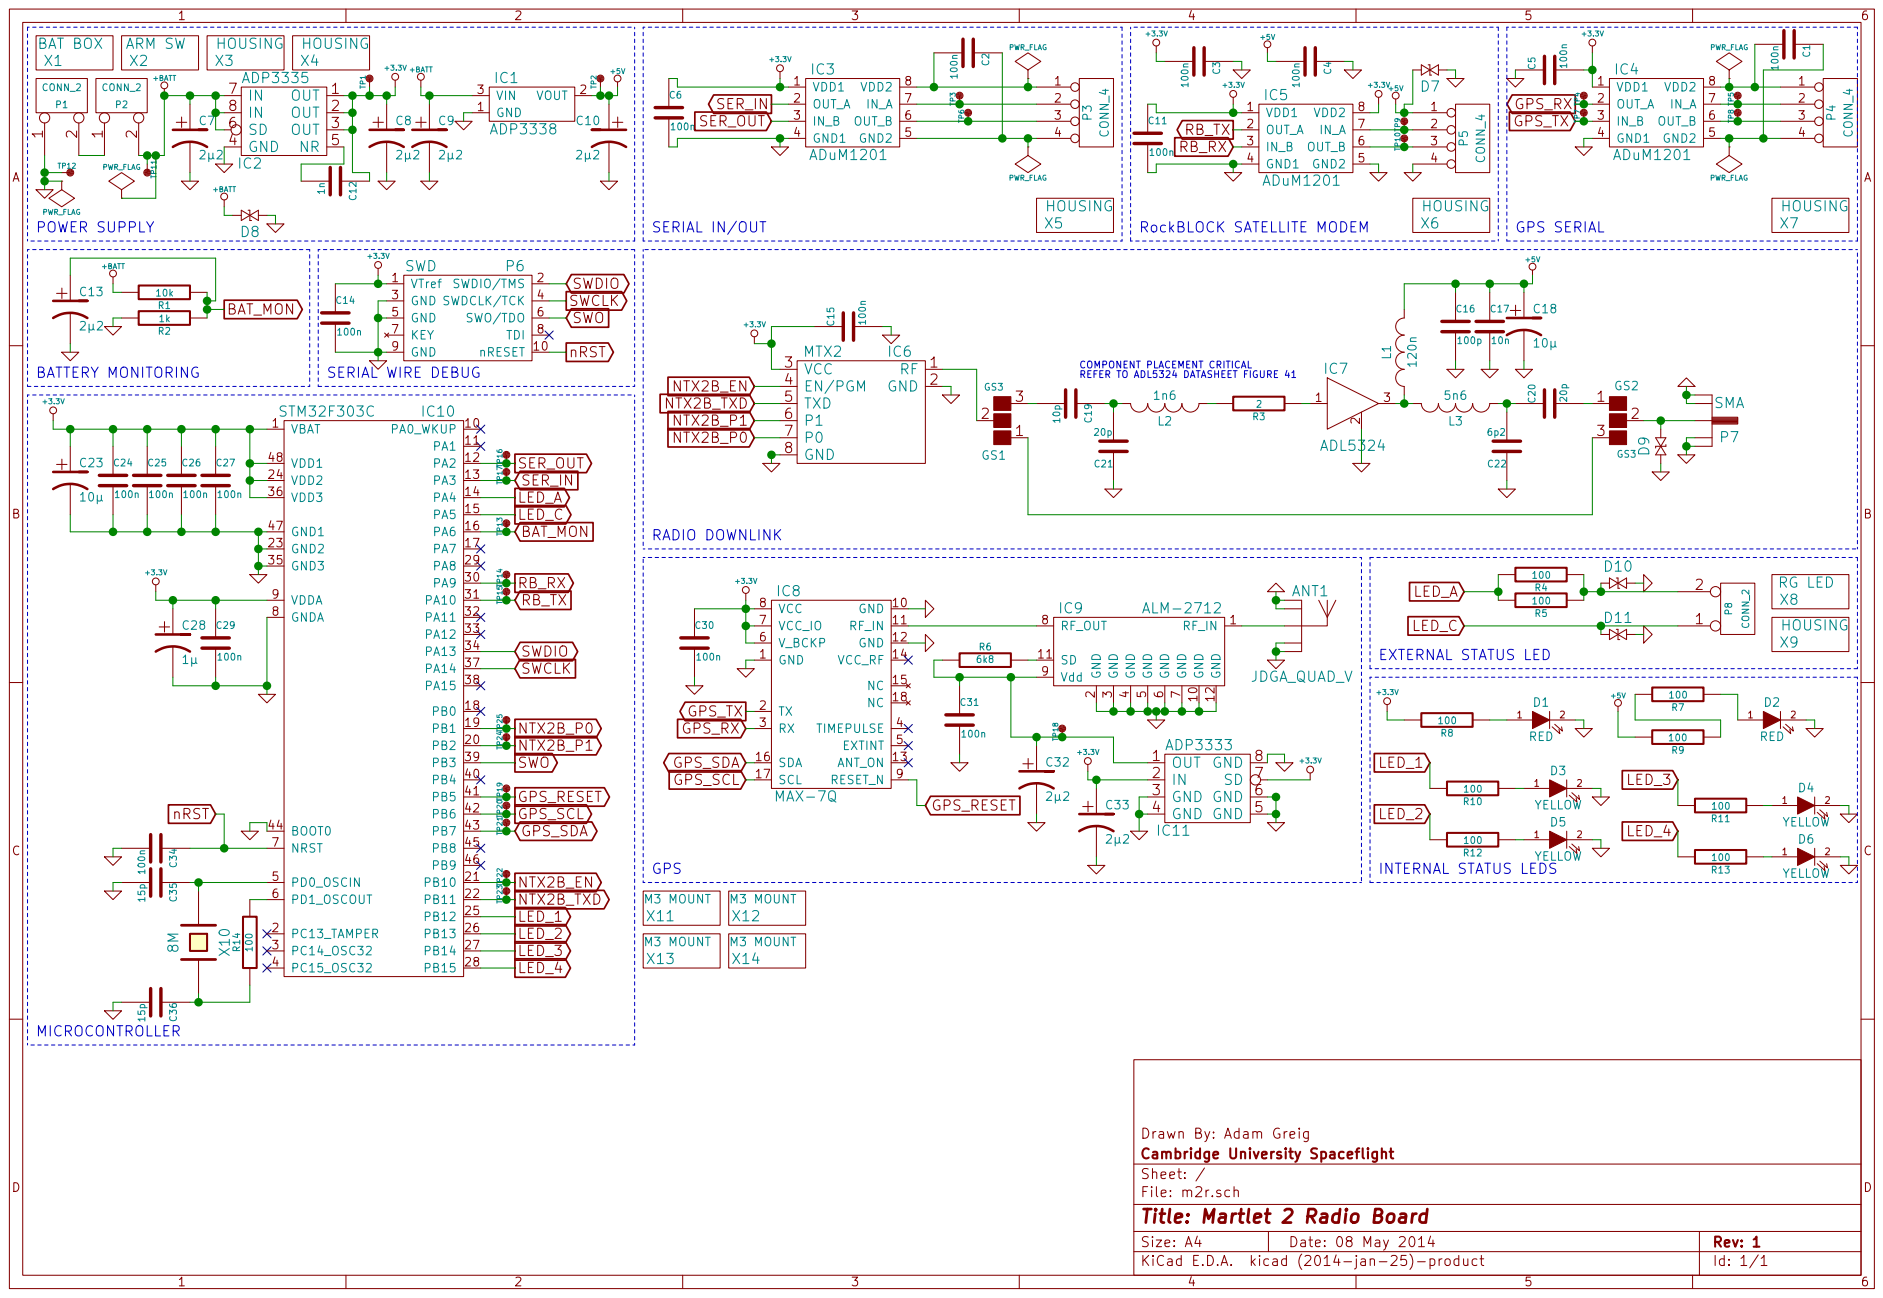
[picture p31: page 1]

7 RF_OUT 8 Vdd 9 GND 10 SD 11 GND 12

File: m2r.sch Sheet: / Cambridge University Spaceflight

Id: 1/1 Title: Martlet 2 Radio Board

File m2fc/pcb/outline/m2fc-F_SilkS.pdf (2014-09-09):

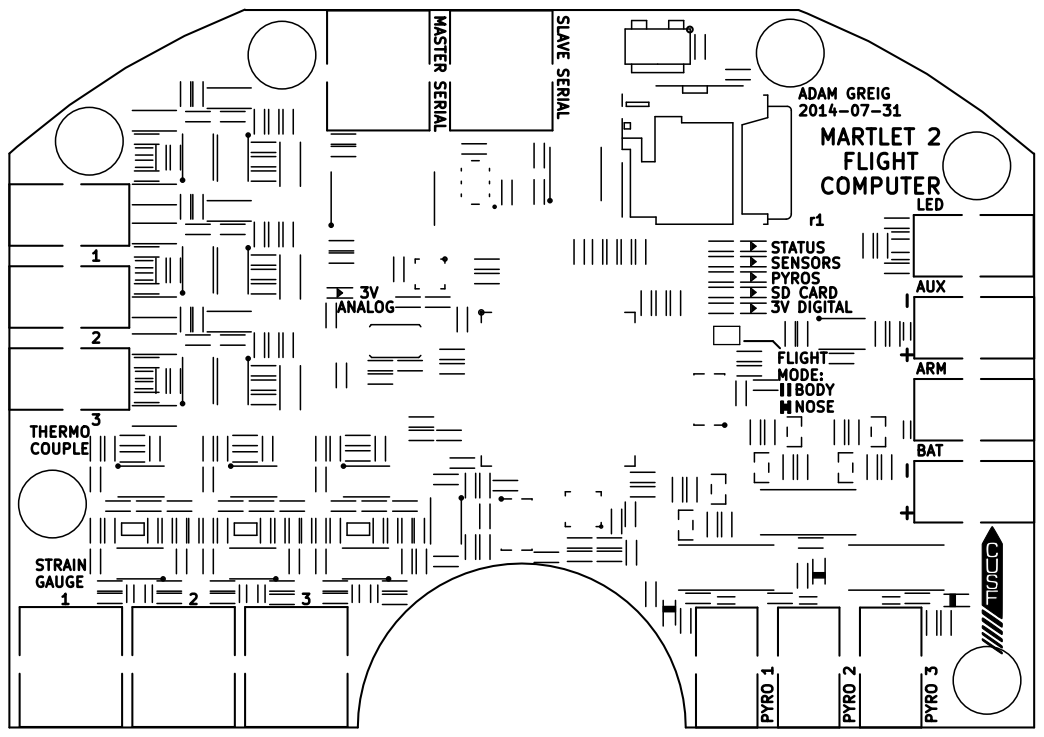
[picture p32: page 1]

STATUS
SENSORS
PYROS
FLIGHT MODE: 3V DIGITAL SD CARD

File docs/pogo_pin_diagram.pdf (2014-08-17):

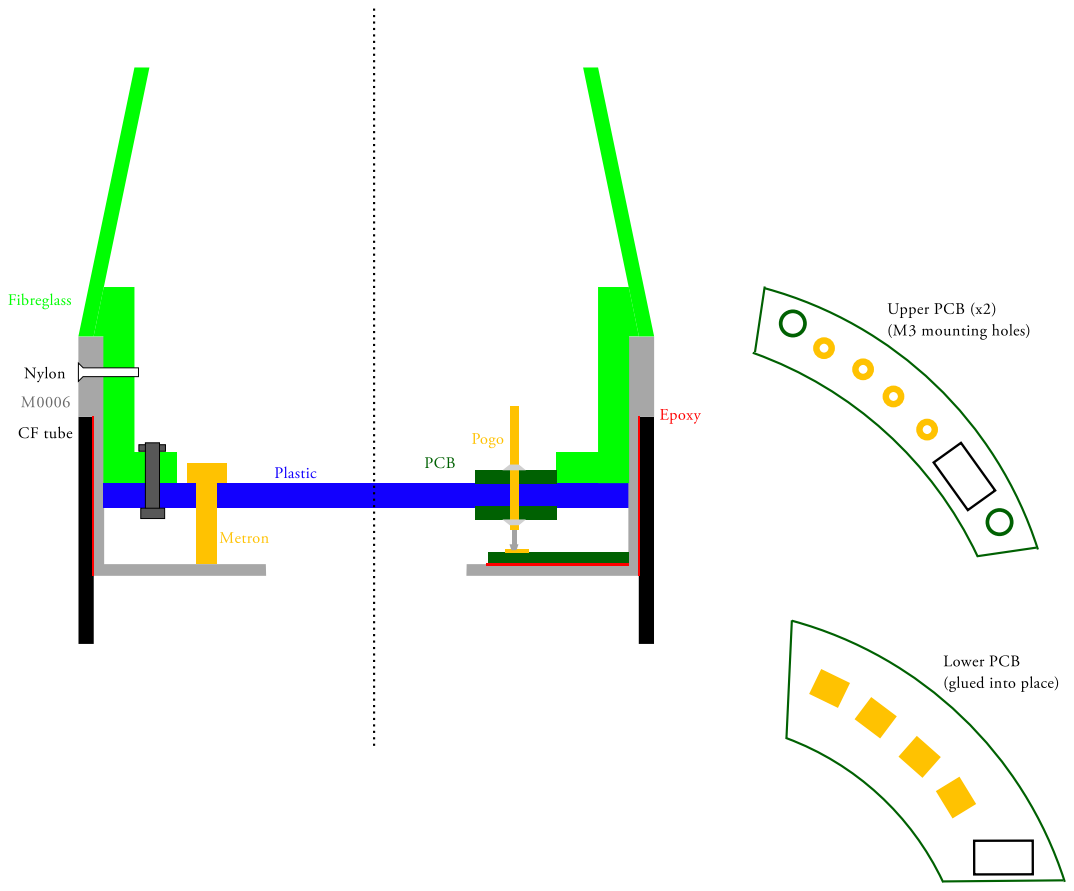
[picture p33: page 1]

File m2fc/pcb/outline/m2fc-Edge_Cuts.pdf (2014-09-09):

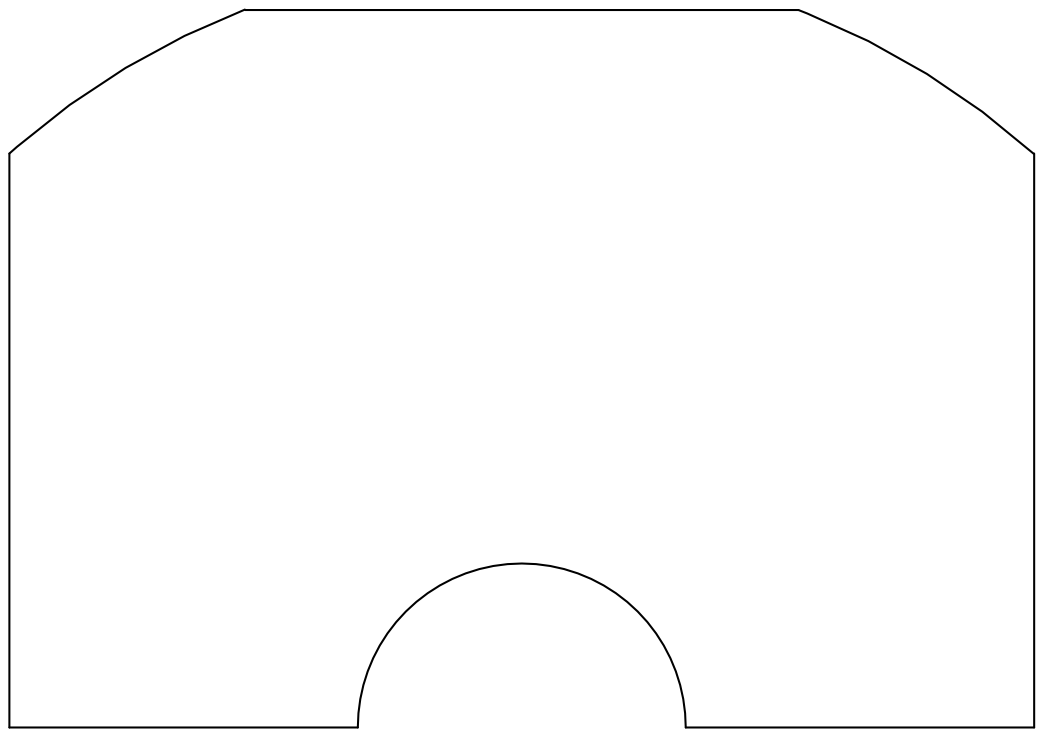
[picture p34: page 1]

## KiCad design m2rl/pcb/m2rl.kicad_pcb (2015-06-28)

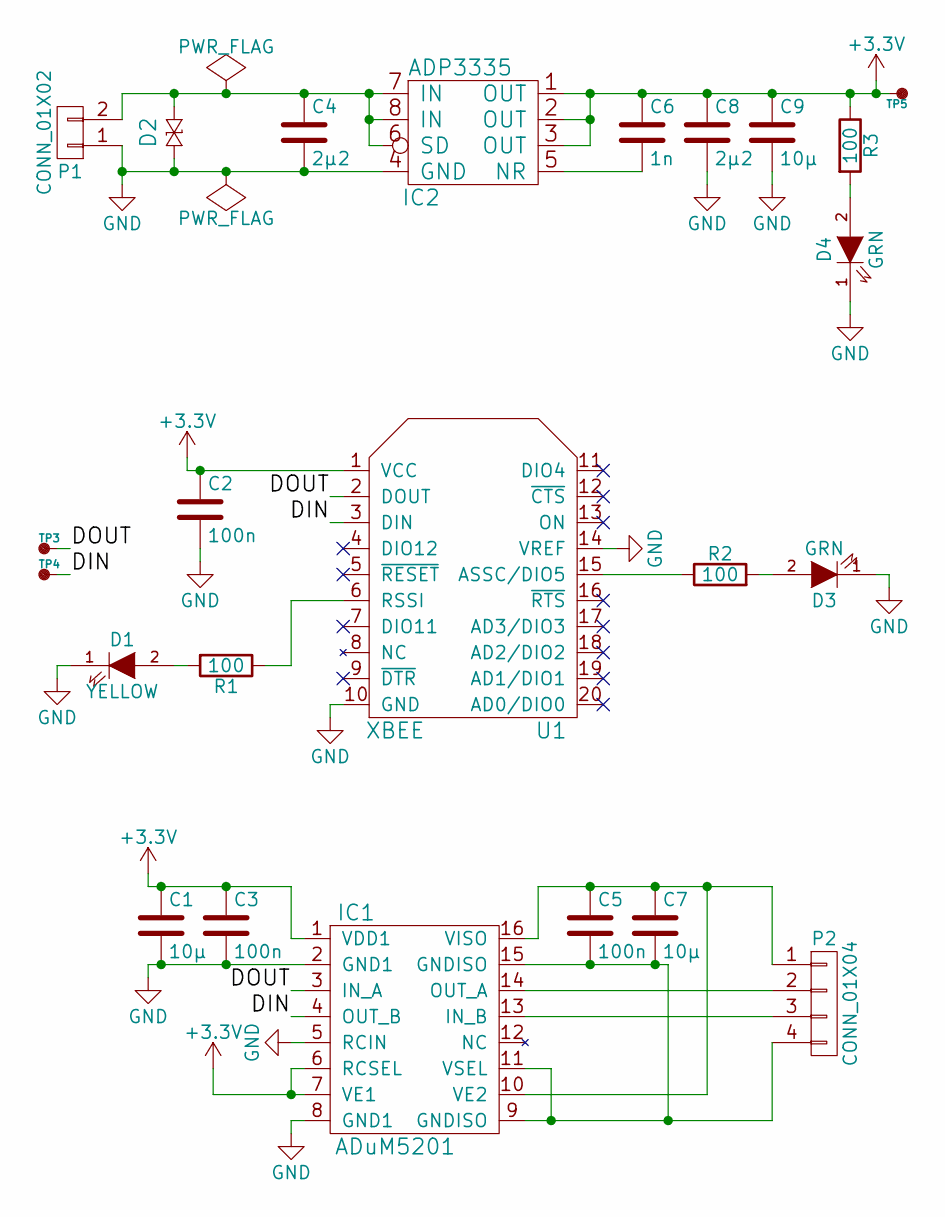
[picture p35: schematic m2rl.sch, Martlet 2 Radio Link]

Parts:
C1, C7, C9: 10µ; C0603; Farnell 2211164
C2, C3, C5: 100n; C0603; Farnell 1759037
C4, C8: 2µ2; C0603; Farnell 2320817
C6: 1n; C0603; Farnell 1414605
D1: YELLOW; LED0603; Farnell 2290330
D2: CGA0402MLC-12G; R0402; Farnell 2368169
D3, D4: GRN; LED0603; Farnell 2290328
IC1: ADuM5201; SOIC16W; Farnell 2067773
IC2: ADP3335; MSOP8; Farnell 2067775
P1: CONN_01X02; S02B-PASK-2; Farnell 1830747
P2: CONN_01X04; S04B-PASK-2; Farnell 1830749
R1, R2, R3: 100; R0603; Farnell 2331989
TP3, TP4, TP5: TESTPAD
U1: XBEE; Farnell 1109732

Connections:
+3V3: C1.1, C2.1, C3.1, C6.1, C8.1, C9.1, IC1.1 (VDD1), IC1.6 (RCSEL), IC1.7 (VE1), IC2.1 (OUT), IC2.2 (OUT), IC2.3 (OUT), R3.1, TP5.1, U1.1 (VCC)
/DIN: IC1.4 (OUT_B), TP4.1, U1.3 (DIN)
/DOUT: IC1.3 (IN_A), TP3.1, U1.2 (DOUT)
GND: C1.2, C2.2, C3.2, C4.2, C8.2, C9.2, D1.1 (K), D2.2, D3.1 (K), D4.1 (K), IC1.2 (GND1), IC1.5 (RCIN), IC1.8 (GND1), IC2.4 (GND), P1.1, U1.10 (GND), U1.14 (VREF)
unnamed: C4.1, D2.1, IC2.6 (SD), IC2.7 (IN), IC2.8 (IN), P1.2
unnamed: C5.1, C7.1, IC1.10 (VE2), IC1.16 (VISO), P2.1
unnamed: C5.2, C7.2, IC1.9 (GNDISO), IC1.11 (VSEL), IC1.15 (GNDISO), P2.4
unnamed: C6.2, IC2.5 (NR)
unnamed: D1.2 (A), R1.2
unnamed: D3.2 (A), R2.2
unnamed: D4.2 (A), R3.2
unnamed: IC1.13 (IN_B), P2.3
unnamed: IC1.14 (OUT_A), P2.2
unnamed: R1.1, U1.6 (RSSI)
unnamed: R2.1, U1.15 (ASSC/DIO5)

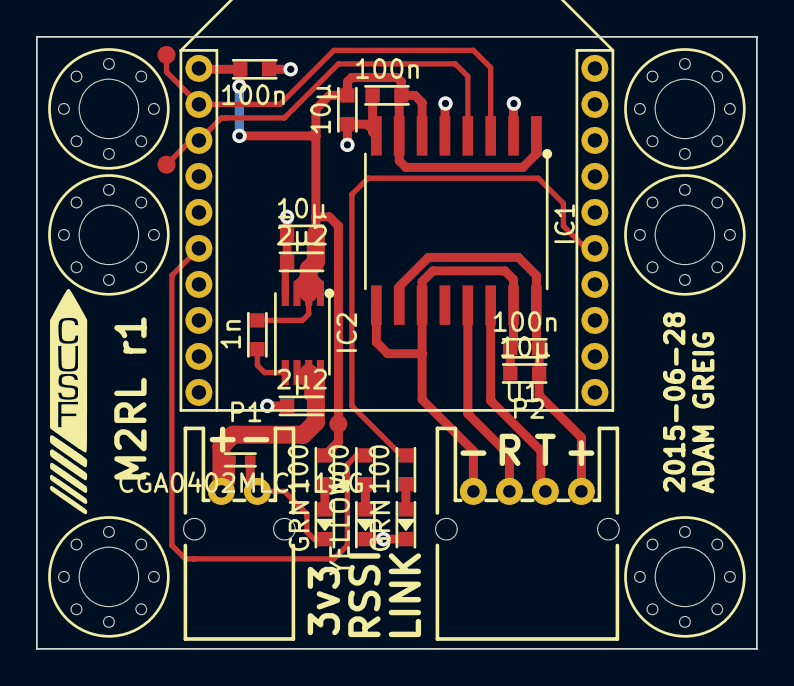
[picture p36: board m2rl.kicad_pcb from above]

Board: 2 copper layers, 40.0 x 34.0 mm, 30 parts (0 on the bottom side), 15 nets.

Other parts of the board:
M3_MOUNT, M3_MOUNT#2, M3_MOUNT#3, M3_MOUNT#4, M3_MOUNT#5, M3_MOUNT#6: VAL**; M3_MOUNT

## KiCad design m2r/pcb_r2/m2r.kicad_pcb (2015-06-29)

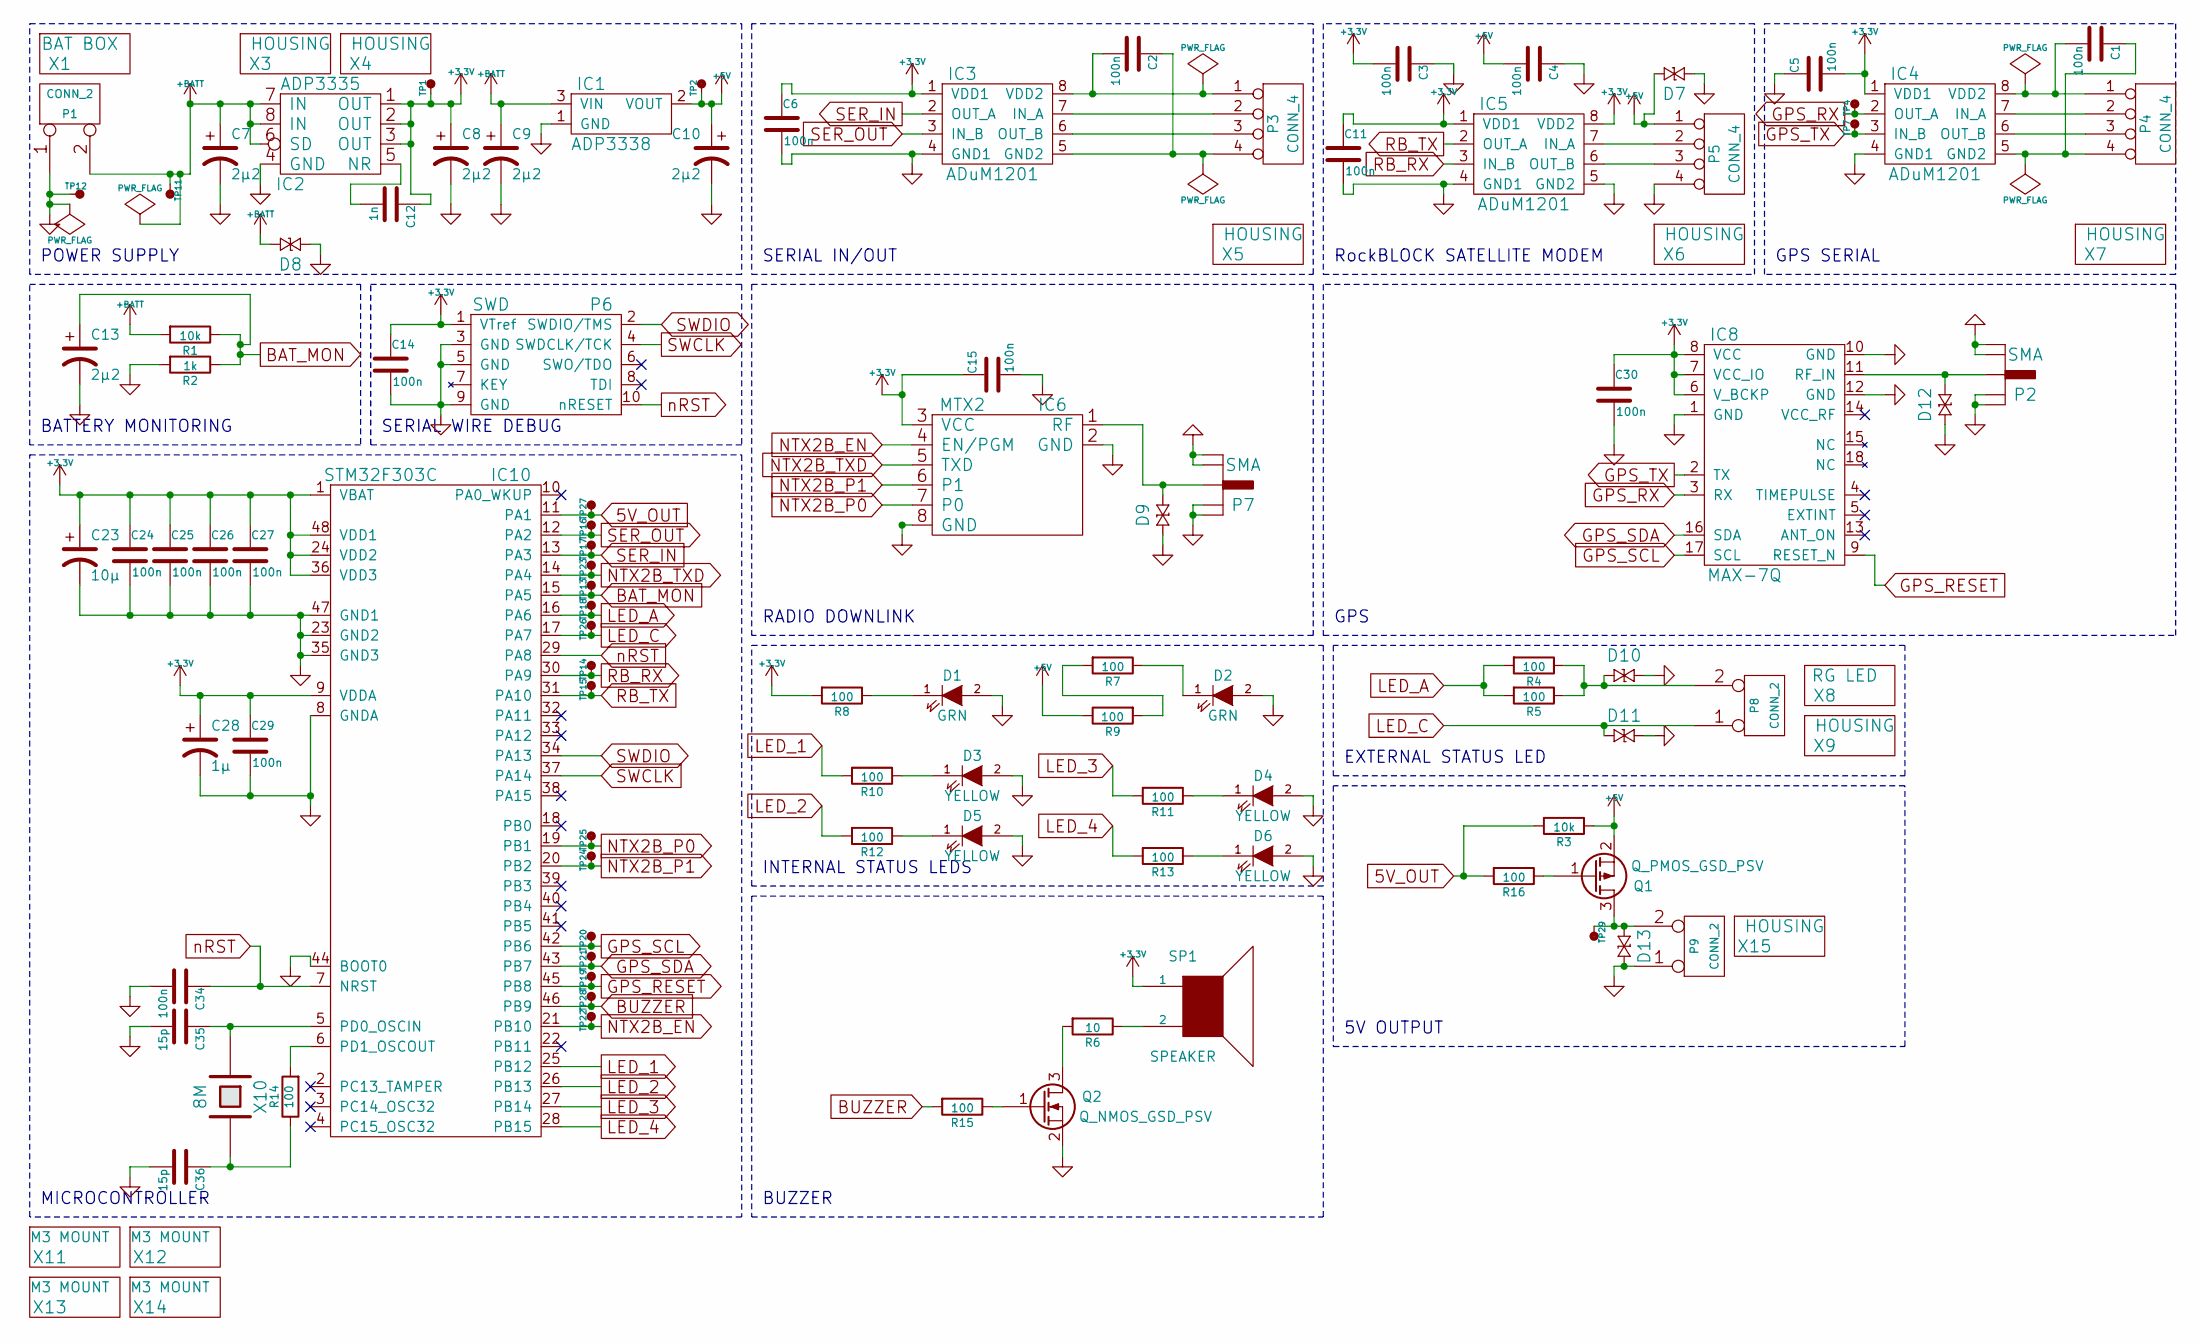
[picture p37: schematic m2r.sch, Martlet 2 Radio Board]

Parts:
C1, C2, C3, C4, C5, C6, C11, C14, C15, C24, C25, C26, C27, C29, C30, C34: 100n; C0603; Farnell 1759037
C7, C8, C9, C10, C13: 2µ2; C0603; Farnell 2320817
C12: 1n; C0603; Farnell 1759088
C23: 10µ; C0603; Farnell 2333026
C28: 1µ; C0603; Farnell 1658211
C35, C36: 15p; C0603; Farnell 1759055
D1, D2: GRN; LED0603; Farnell 2290328
D3, D4, D5, D6: YELLOW; LED0603; Farnell 2290330
D7, D8, D9, D10, D11, D12, D13: CGA0402MLC-12G; R0402; Farnell 2368169
IC1: ADP3338; SOT223; Farnell 1651284
IC2: ADP3335; MSOP8; Farnell 2067775
IC3, IC4, IC5: ADuM1201; SOIC8; Farnell 1078200
IC6: MTX2
IC8: MAX-7Q
IC10: STM32F303C; LQFP48; Farnell 2333361
P1, P8, P9: CONN_2; S02B-PASK-2; Farnell 1830747
P2, P7: SMA; SMA-142-0701-801; Farnell 1608592
P3, P4, P5: CONN_4; S04B-PASK-2
P6: SWD; FTSH-105-01-F-D-K; Farnell 2308436
Q1: Q_PMOS_GSD_PSV; SOT-23; Farnell 1894738
Q2: Q_NMOS_GSD_PSV; SOT-23; Farnell 1510761
R1, R3: 10k; R0603; Farnell 2332016
R2: 1k; R0603; Farnell 2331727
R4, R5, R7, R8, R9, R10, R11, R12, R13, R14, R15, R16: 100; R0603; Farnell 2331989
R6: 10; R0603; Farnell 2331975
SP1: SPEAKER; ABI-042-RC; Farnell 1827949
TP1, TP2, TP4, TP7, TP11, TP12, TP13, TP14, TP15, TP16, TP17, TP18, TP19, TP20, TP21, TP22, TP23, TP24, TP25, TP26, TP27, TP28, TP29: TESTPAD
X1: BAT BOX; Farnell BT01732
X3, X4, X9, X15: HOUSING; Farnell 1830726
X5, X6, X7: HOUSING; Farnell 1830729
X8: RG LED; Farnell 1142488
X10: 8M; XTAL50x32; Farnell 2101329
X11, X12, X13, X14: M3 MOUNT; M3_MOUNT

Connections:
5V_OUT: IC10.11 (PA1), R3.2, R16.2, TP27.1
+3V3: C3.2, C5.2, C6.1, C8.1, C11.1, C12.1, C14.1, C15.1, C23.1, C24.1, C25.1, C26.1, C27.1, C28.1, C29.1, C30.1, IC2.1 (OUT), IC2.2 (OUT), IC2.3 (OUT), IC3.1 (VDD1), IC4.1 (VDD1), IC5.1 (VDD1), IC5.8 (VDD2), IC6.3 (VCC), IC8.6 (V_BCKP), IC8.7 (VCC_IO), IC8.8 (VCC), IC10.1 (VBAT), IC10.9 (VDDA), IC10.24 (VDD2), IC10.36 (VDD3), IC10.48 (VDD1), P6.1 (VTref), R8.2, SP1.1, TP1.1
+5V: C4.2, C10.1, D7.1, IC1.2 (VOUT), P5.1, Q1.2 (S), R3.1, R9.1, TP2.1
+BATT: C7.1, C9.1, D8.1, IC1.3 (VIN), IC2.6 (SD), IC2.7 (IN), IC2.8 (IN), P1.2 (PM), R1.2, TP11.1
BAT_MON: C13.1, IC10.15 (PA5), R1.1, R2.1, TP13.1
BUZZER: IC10.46 (PB9), R15.2, TP28.1
GND: C3.1, C4.1, C5.1, C6.2, C7.2, C8.2, C9.2, C10.2, C11.2, C13.2, C14.2, C15.2, C23.2, C24.2, C25.2, C26.2, C27.2, C28.2, C29.2, C30.2, C34.2, C35.2, C36.2, D1.2 (A), D2.2 (A), D3.2 (A), D4.2 (A), D5.2 (A), D6.2 (A), D7.2, D8.2, D9.2, D10.1, D11.1, D12.2, D13.1, IC1.1 (GND), IC2.4 (GND), IC3.4 (GND1), IC4.4 (GND1), IC5.4 (GND1), IC5.5 (GND2), IC6.2 (GND), IC6.8 (GND), IC8.1 (GND), IC8.10 (GND), IC8.12 (GND), IC10.8 (GNDA), IC10.23 (GND2), IC10.35 (GND3), IC10.44 (BOOT0), IC10.47 (GND1), P1.1, P2.2 (GND), P2.3 (GND), P2.4 (GND), P2.5 (GND), P5.4, P6.3 (GND), P6.5 (GND), P6.9 (GND), P7.2 (GND), P7.3 (GND), P7.4 (GND), P7.5 (GND), P9.1, Q2.2 (S), R2.2, TP12.1
GPS_RESET: IC8.9 (RESET_N), IC10.45 (PB8), TP19.1
GPS_RX: IC4.2 (OUT_A), IC8.3 (RX), TP4.1
GPS_SCL: IC8.17 (SCL), IC10.42 (PB6), TP20.1
GPS_SDA: IC8.16 (SDA), IC10.43 (PB7), TP21.1
GPS_TX: IC4.3 (IN_B), IC8.2 (TX), TP7.1
LED_1: IC10.25 (PB12), R10.2
LED_2: IC10.26 (PB13), R12.2
LED_3: IC10.27 (PB14), R11.2
LED_4: IC10.28 (PB15), R13.2
LED_A: IC10.16 (PA6), R4.2, R5.2, TP18.1
LED_C: D11.2, IC10.17 (PA7), P8.1, TP26.1
NTX2B_EN: IC6.4 (EN/PGM), IC10.21 (PB10), TP22.1
NTX2B_P0: IC6.7 (P0), IC10.19 (PB1), TP25.1
NTX2B_P1: IC6.6 (P1), IC10.20 (PB2), TP24.1
NTX2B_TXD: IC6.5 (TXD), IC10.14 (PA4), TP23.1
unnamed: C1.1, IC4.5 (GND2), P4.4
unnamed: C1.2, IC4.8 (VDD2), P4.1
unnamed: C2.1, IC3.5 (GND2), P3.4
unnamed: C2.2, IC3.8 (VDD2), P3.1
unnamed: C12.2, IC2.5 (NR)
unnamed: C35.1, IC10.5 (PD0_OSCIN), X10.1
unnamed: C36.1, R14.1, X10.2
unnamed: D1.1 (K), R8.1
unnamed: D2.1 (K), R7.1
unnamed: D3.1 (K), R10.1
unnamed: D4.1 (K), R11.1
unnamed: D5.1 (K), R12.1
unnamed: D6.1 (K), R13.1
unnamed: D9.1, IC6.1 (RF), P7.1 (RF)
unnamed: D10.2, P8.2 (PM), R4.1, R5.1
unnamed: D12.1, IC8.11 (RF_IN), P2.1 (RF)
unnamed: D13.2, P9.2 (PM), Q1.3 (D), TP29.1
unnamed: IC3.6 (OUT_B), P3.3
unnamed: IC3.7 (IN_A), P3.2
unnamed: IC4.6 (OUT_B), P4.3
unnamed: IC4.7 (IN_A), P4.2
unnamed: IC5.6 (OUT_B), P5.3
unnamed: IC5.7 (IN_A), P5.2
unnamed: IC10.6 (PD1_OSCOUT), R14.2
unnamed: Q1.1 (G), R16.1
unnamed: Q2.1 (G), R15.1
unnamed: Q2.3 (D), R6.2
unnamed: R6.1, SP1.2
unnamed: R7.2, R9.2
RB_RX: IC5.3 (IN_B), IC10.30 (PA9), TP14.1
RB_TX: IC5.2 (OUT_A), IC10.31 (PA10), TP15.1
SER_IN: IC3.2 (OUT_A), IC10.13 (PA3), TP17.1
SER_OUT: IC3.3 (IN_B), IC10.12 (PA2), TP16.1
SWCLK: IC10.37 (PA14), P6.4 (SWDCLK/TCK)
SWDIO: IC10.34 (PA13), P6.2 (SWDIO/TMS)
nRST: C34.1, IC10.7 (NRST), IC10.29 (PA8), P6.10 (nRESET)

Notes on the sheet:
POWER SUPPLY
BATTERY MONITORING
SERIAL WIRE DEBUG
SERIAL IN/OUT
RockBLOCK SATELLITE MODEM
RADIO DOWNLINK
GPS
MICROCONTROLLER
EXTERNAL STATUS LED
INTERNAL STATUS LEDS
GPS SERIAL
BUZZER
5V OUTPUT

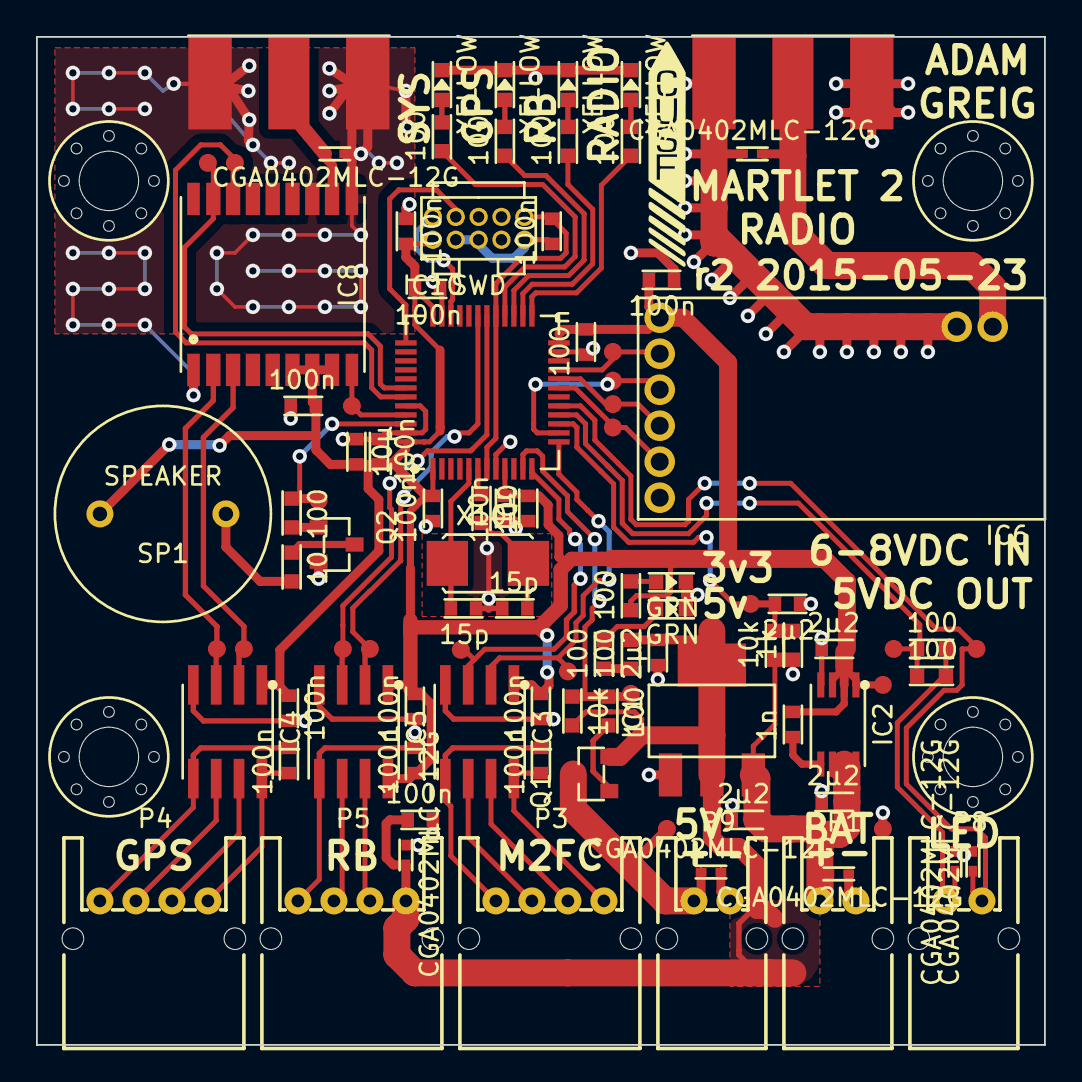
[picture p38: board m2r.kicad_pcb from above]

Board: 2 copper layers, 56.0 x 56.0 mm, 103 parts (0 on the bottom side), 58 nets.

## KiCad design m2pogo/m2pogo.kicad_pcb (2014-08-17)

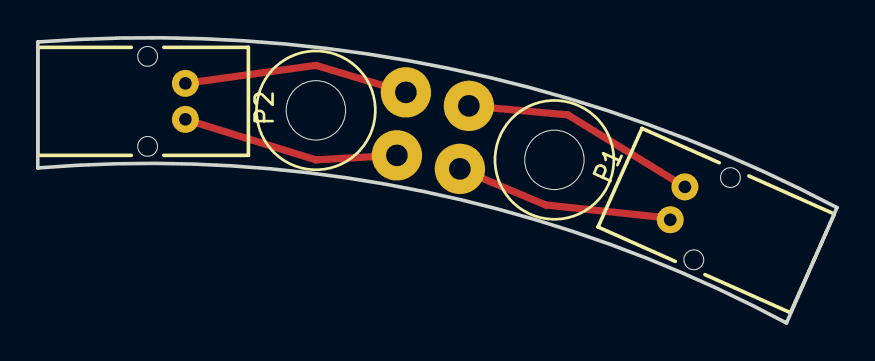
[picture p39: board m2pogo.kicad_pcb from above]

Board: 2 copper layers, 44.4 x 15.8 mm, 8 parts (0 on the bottom side), 4 nets.

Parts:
P1, P2: CONN_2; S02B-PASK-2
P3, P4, P5, P6: CONN_1; POGO
X3, X4: MOUNT; M3_MOUNT

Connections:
unnamed: P1.1, P4.1
unnamed: P1.2, P3.1
unnamed: P2.1, P6.1
unnamed: P2.2, P5.1

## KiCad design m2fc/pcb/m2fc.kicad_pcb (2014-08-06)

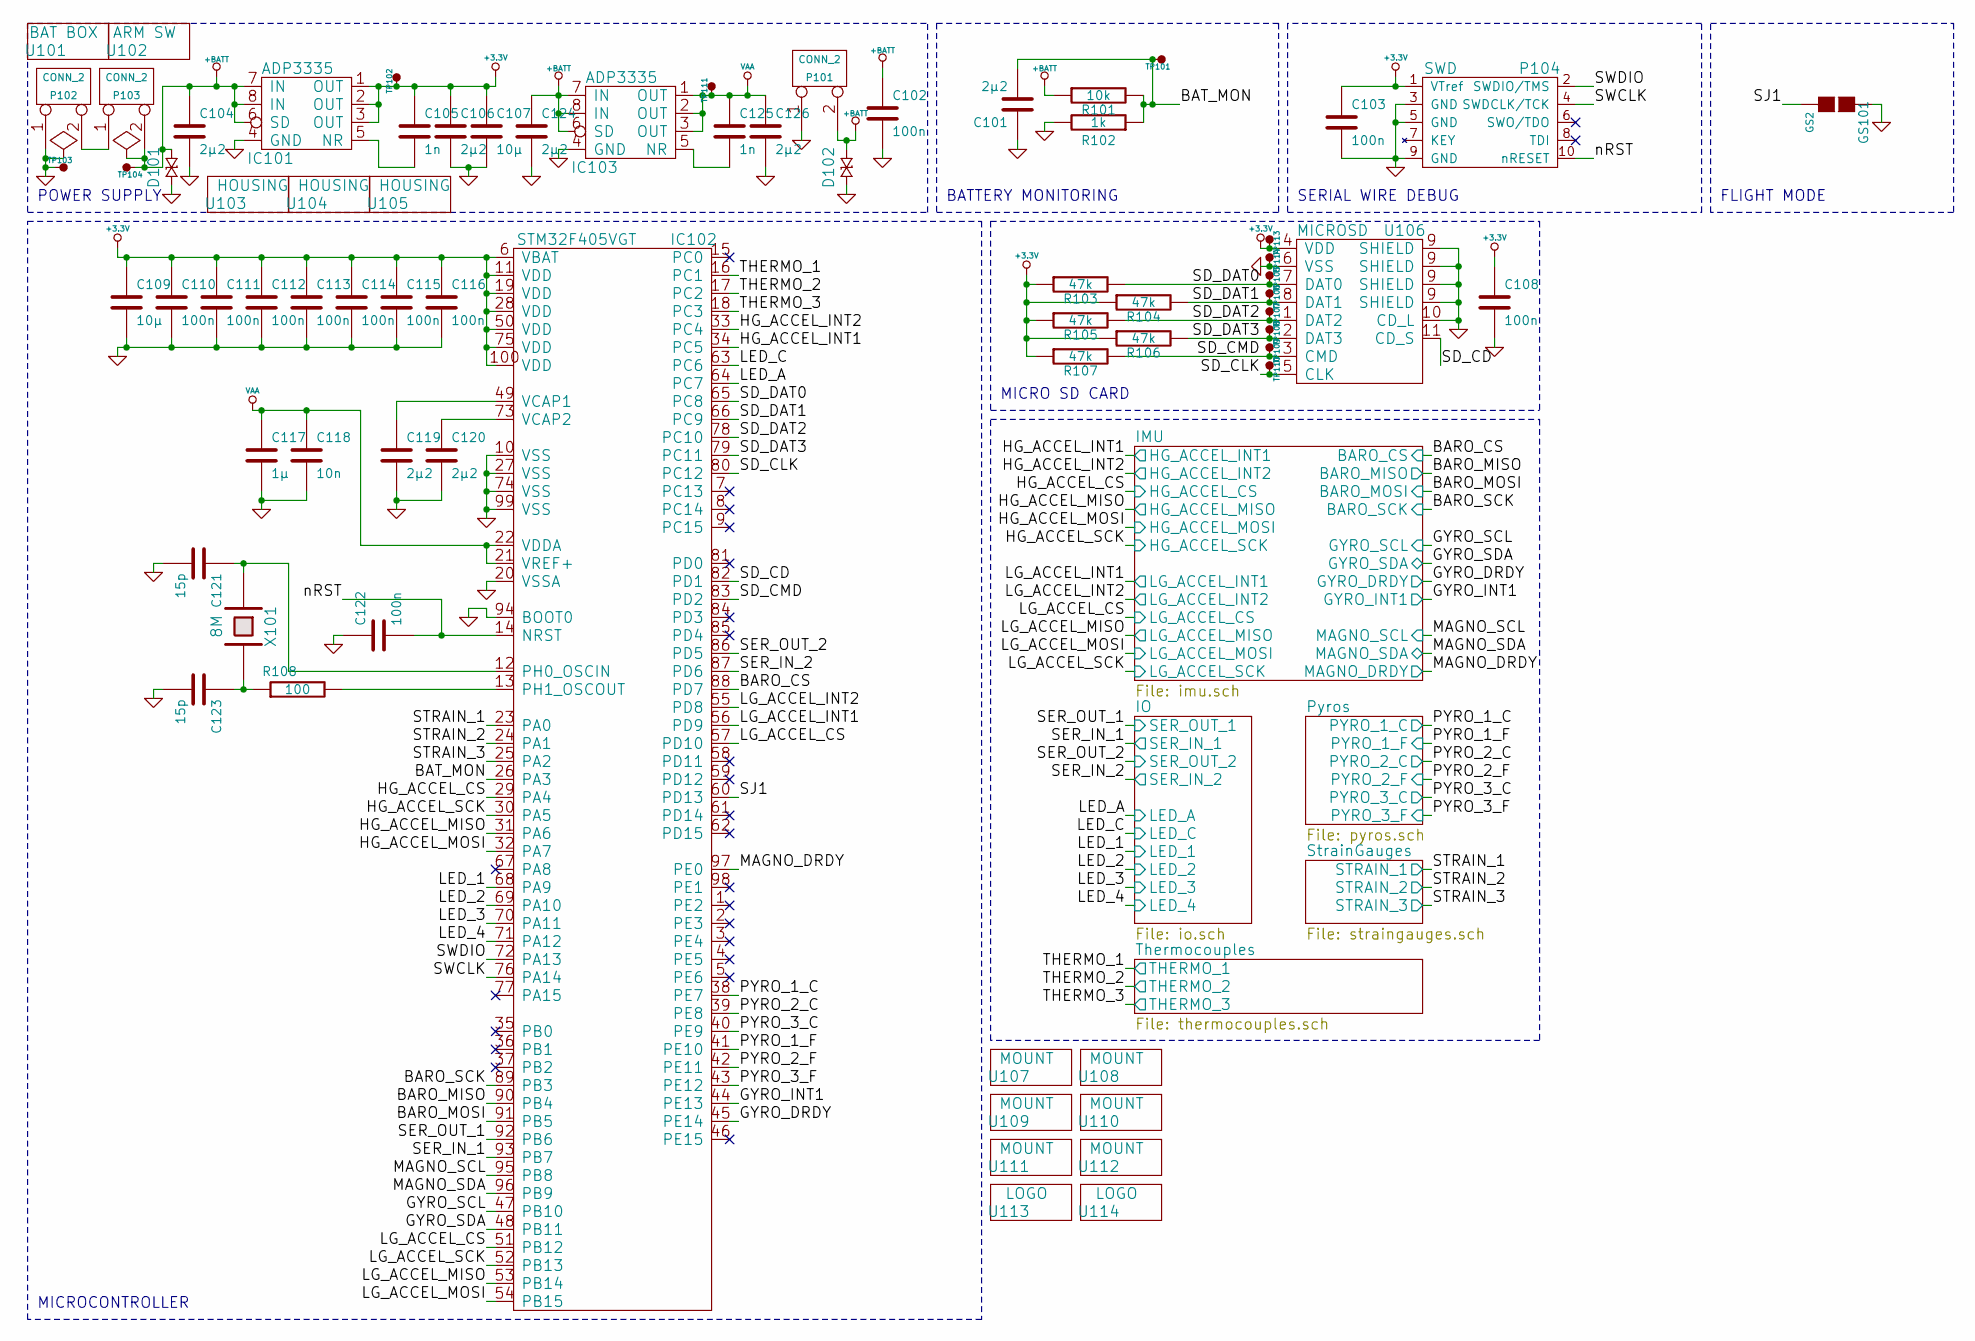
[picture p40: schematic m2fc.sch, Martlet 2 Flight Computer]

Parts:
C101, C104, C106, C119, C120, C124, C126: 2µ2; C0603; Farnell 2320817
C102, C103, C108, C110, C111, C112, C113, C114, C115, C116, C122: 100n; C0603; Farnell 1759037
C105, C125: 1n; C0603; Farnell 1414605
C107, C109: 10µ; C0603; Farnell 2211164
C117: 1µ; C0603; Farnell 2346895
C118: 10n; C0603; Farnell 2112704
C121, C123: 15p; C0603; Farnell 1759055
D101, D102: CGA0402MLC-12G; R0402; Farnell 2368169
GS101: GS2
IC101, IC103: ADP3335; MSOP8; Farnell 2067775
IC102: STM32F405VGT; LQFP100; Farnell 2393648
P101, P102, P103: CONN_2; S02B-PASK-2; Farnell 1830747
P104: SWD; FTSH-105-01-F-D-K; Farnell 1667759
R101: 10k; R0603; Farnell 2332016
R102: 1k; R0603; Farnell 2116678
R103, R104, R105, R106, R107: 47k; R0603; Farnell 2332025
R108: 100; R0603; Farnell 2331989
TP101, TP102, TP103, TP104, TP105, TP106, TP107, TP108, TP109, TP110, TP111, TP113, TP114: TESTPAD
U101: BAT BOX; Farnell BT01732
U102: ARM SW; Farnell SW04244
U103, U104, U105: HOUSING; Farnell 1830726
U106: MICROSD; Farnell 2334075
U107, U108, U109, U110, U111, U112: MOUNT; M3_MOUNT
U113: LOGO; cusf_logo_full
U114: LOGO; cusf_logo_small
X101: 8M; XTAL50x32; Farnell 2101329

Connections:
+3.3V: C103.1, C105.1, C106.1, C107.1, C108.1, C109.1, C110.1, C111.1, C112.1, C113.1, C114.1, C115.1, C116.1, IC101.1 (OUT), IC101.2 (OUT), IC101.3 (OUT), IC102.6 (VBAT), IC102.11 (VDD), IC102.19 (VDD), IC102.28 (VDD), IC102.50 (VDD), IC102.75 (VDD), IC102.100 (VDD), P104.1 (VTref), R103.1, R104.1, R105.1, R106.1, R107.1, TP102.1, TP113.1, U106.4 (VDD); also elsewhere on the board
+BATT: C102.1, C104.1, C124.1, D101.1, D102.1, IC101.6 (SD), IC101.7 (IN), IC101.8 (IN), IC103.6 (SD), IC103.7 (IN), IC103.8 (IN), P101.2 (PM), P103.2 (PM), R101.1, TP104.1; also elsewhere on the board
/BAT_MON: C101.2, IC102.26 (PA3), R101.2, R102.1, TP101.1
/IMU/BARO_CS: IC102.88 (PD7); also elsewhere on the board
/IMU/BARO_MISO: IC102.90 (PB4); also elsewhere on the board
/IMU/BARO_MOSI: IC102.91 (PB5); also elsewhere on the board
/IMU/BARO_SCK: IC102.89 (PB3); also elsewhere on the board
/IMU/GYRO_DRDY: IC102.45 (PE14); also elsewhere on the board
/IMU/GYRO_INT1: IC102.44 (PE13); also elsewhere on the board
/IMU/GYRO_SCL: IC102.47 (PB10); also elsewhere on the board
/IMU/GYRO_SDA: IC102.48 (PB11); also elsewhere on the board
/IMU/HG_ACCEL_CS: IC102.29 (PA4); also elsewhere on the board
/IMU/HG_ACCEL_INT1: IC102.34 (PC5); also elsewhere on the board
/IMU/HG_ACCEL_INT2: IC102.33 (PC4); also elsewhere on the board
/IMU/HG_ACCEL_MISO: IC102.31 (PA6); also elsewhere on the board
/IMU/HG_ACCEL_MOSI: IC102.32 (PA7); also elsewhere on the board
/IMU/HG_ACCEL_SCK: IC102.30 (PA5); also elsewhere on the board
/IMU/LG_ACCEL_CS: IC102.51 (PB12), IC102.57 (PD10); also elsewhere on the board
/IMU/LG_ACCEL_INT1: IC102.56 (PD9); also elsewhere on the board
/IMU/LG_ACCEL_INT2: IC102.55 (PD8); also elsewhere on the board
/IMU/LG_ACCEL_MISO: IC102.53 (PB14); also elsewhere on the board
/IMU/LG_ACCEL_MOSI: IC102.54 (PB15); also elsewhere on the board
/IMU/LG_ACCEL_SCK: IC102.52 (PB13); also elsewhere on the board
/IMU/MAGNO_DRDY: IC102.97 (PE0); also elsewhere on the board
/IMU/MAGNO_SCL: IC102.95 (PB8); also elsewhere on the board
/IMU/MAGNO_SDA: IC102.96 (PB9); also elsewhere on the board
/IO/LED_1: IC102.68 (PA9); also elsewhere on the board
/IO/LED_2: IC102.69 (PA10); also elsewhere on the board
/IO/LED_3: IC102.70 (PA11); also elsewhere on the board
/IO/LED_4: IC102.71 (PA12); also elsewhere on the board
/IO/LED_A: IC102.64 (PC7); also elsewhere on the board
/IO/LED_C: IC102.63 (PC6); also elsewhere on the board
/IO/SER_IN_1: IC102.93 (PB7); also elsewhere on the board
/IO/SER_IN_2: IC102.87 (PD6); also elsewhere on the board
/IO/SER_OUT_1: IC102.92 (PB6); also elsewhere on the board
/IO/SER_OUT_2: IC102.86 (PD5); also elsewhere on the board
/Pyros/PYRO_1_C: IC102.38 (PE7); also elsewhere on the board
/Pyros/PYRO_1_F: IC102.41 (PE10); also elsewhere on the board
/Pyros/PYRO_2_C: IC102.39 (PE8); also elsewhere on the board
/Pyros/PYRO_2_F: IC102.42 (PE11); also elsewhere on the board
/Pyros/PYRO_3_C: IC102.40 (PE9); also elsewhere on the board
/Pyros/PYRO_3_F: IC102.43 (PE12); also elsewhere on the board
/SD_CD: IC102.82 (PD1), U106.11 (CD_S)
/SD_CLK: IC102.80 (PC12), TP110.1, U106.5 (CLK)
/SD_CMD: IC102.83 (PD2), R107.2, TP109.1, U106.3 (CMD)
/SD_DAT0: IC102.65 (PC8), R103.2, TP105.1, U106.7 (DAT0)
/SD_DAT1: IC102.66 (PC9), R104.2, TP106.1, U106.8 (DAT1)
/SD_DAT2: IC102.78 (PC10), R105.2, TP107.1, U106.1 (DAT2)
/SD_DAT3: IC102.79 (PC11), R106.2, TP108.1, U106.2 (DAT3)
/SJ1: GS101.2 (G2), IC102.60 (PD13)
/SWCLK: IC102.76 (PA14), P104.4 (SWDCLK/TCK)
/SWDIO: IC102.72 (PA13), P104.2 (SWDIO/TMS)
/StrainGauges/STRAIN_1: IC102.23 (PA0); also elsewhere on the board
/StrainGauges/STRAIN_2: IC102.24 (PA1); also elsewhere on the board
/StrainGauges/STRAIN_3: IC102.25 (PA2); also elsewhere on the board
/Thermocouples/THERMO_1: IC102.16 (PC1); also elsewhere on the board
/Thermocouples/THERMO_2: IC102.17 (PC2); also elsewhere on the board
/Thermocouples/THERMO_3: IC102.18 (PC3); also elsewhere on the board
/nRST: C122.2, IC102.14 (NRST), P104.10 (nRESET)
GND: C101.1, C102.2, C103.2, C104.2, C106.2, C107.2, C108.2, C109.2, C110.2, C111.2, C112.2, C113.2, C114.2, C115.2, C116.2, C117.2, C118.2, C119.2, C120.2, C121.2, C122.1, C123.2, C124.2, C126.2, D101.2, D102.2, GS101.1 (G1), IC101.4 (GND), IC102.10 (VSS), IC102.20 (VSSA), IC102.27 (VSS), IC102.74 (VSS), IC102.94 (BOOT0), IC102.99 (VSS), IC103.4 (GND), P101.1, P102.1, P104.3 (GND), P104.5 (GND), P104.9 (GND), R102.2, TP103.1, TP114.1, U106.6 (VSS), U106.9 (SHIELD), U106.10 (CD_L); also elsewhere on the board
unnamed: C105.2, IC101.5 (NR)
unnamed: C119.1, IC102.49 (VCAP1)
unnamed: C120.1, IC102.73 (VCAP2)
unnamed: C121.1, IC102.12 (PH0_OSCIN), X101.1
unnamed: C123.1, R108.1, X101.2
unnamed: C125.2, IC103.5 (NR)
unnamed: IC102.13 (PH1_OSCOUT), R108.2
unnamed: P102.2 (PM), P103.1
VAA: C117.1, C118.1, C125.1, C126.1, IC102.21 (VREF+), IC102.22 (VDDA), IC103.1 (OUT), IC103.2 (OUT), IC103.3 (OUT), TP111.1; also elsewhere on the board

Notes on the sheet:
MICROCONTROLLER
POWER SUPPLY
BATTERY MONITORING
SERIAL WIRE DEBUG
MICRO SD CARD
FLIGHT MODE

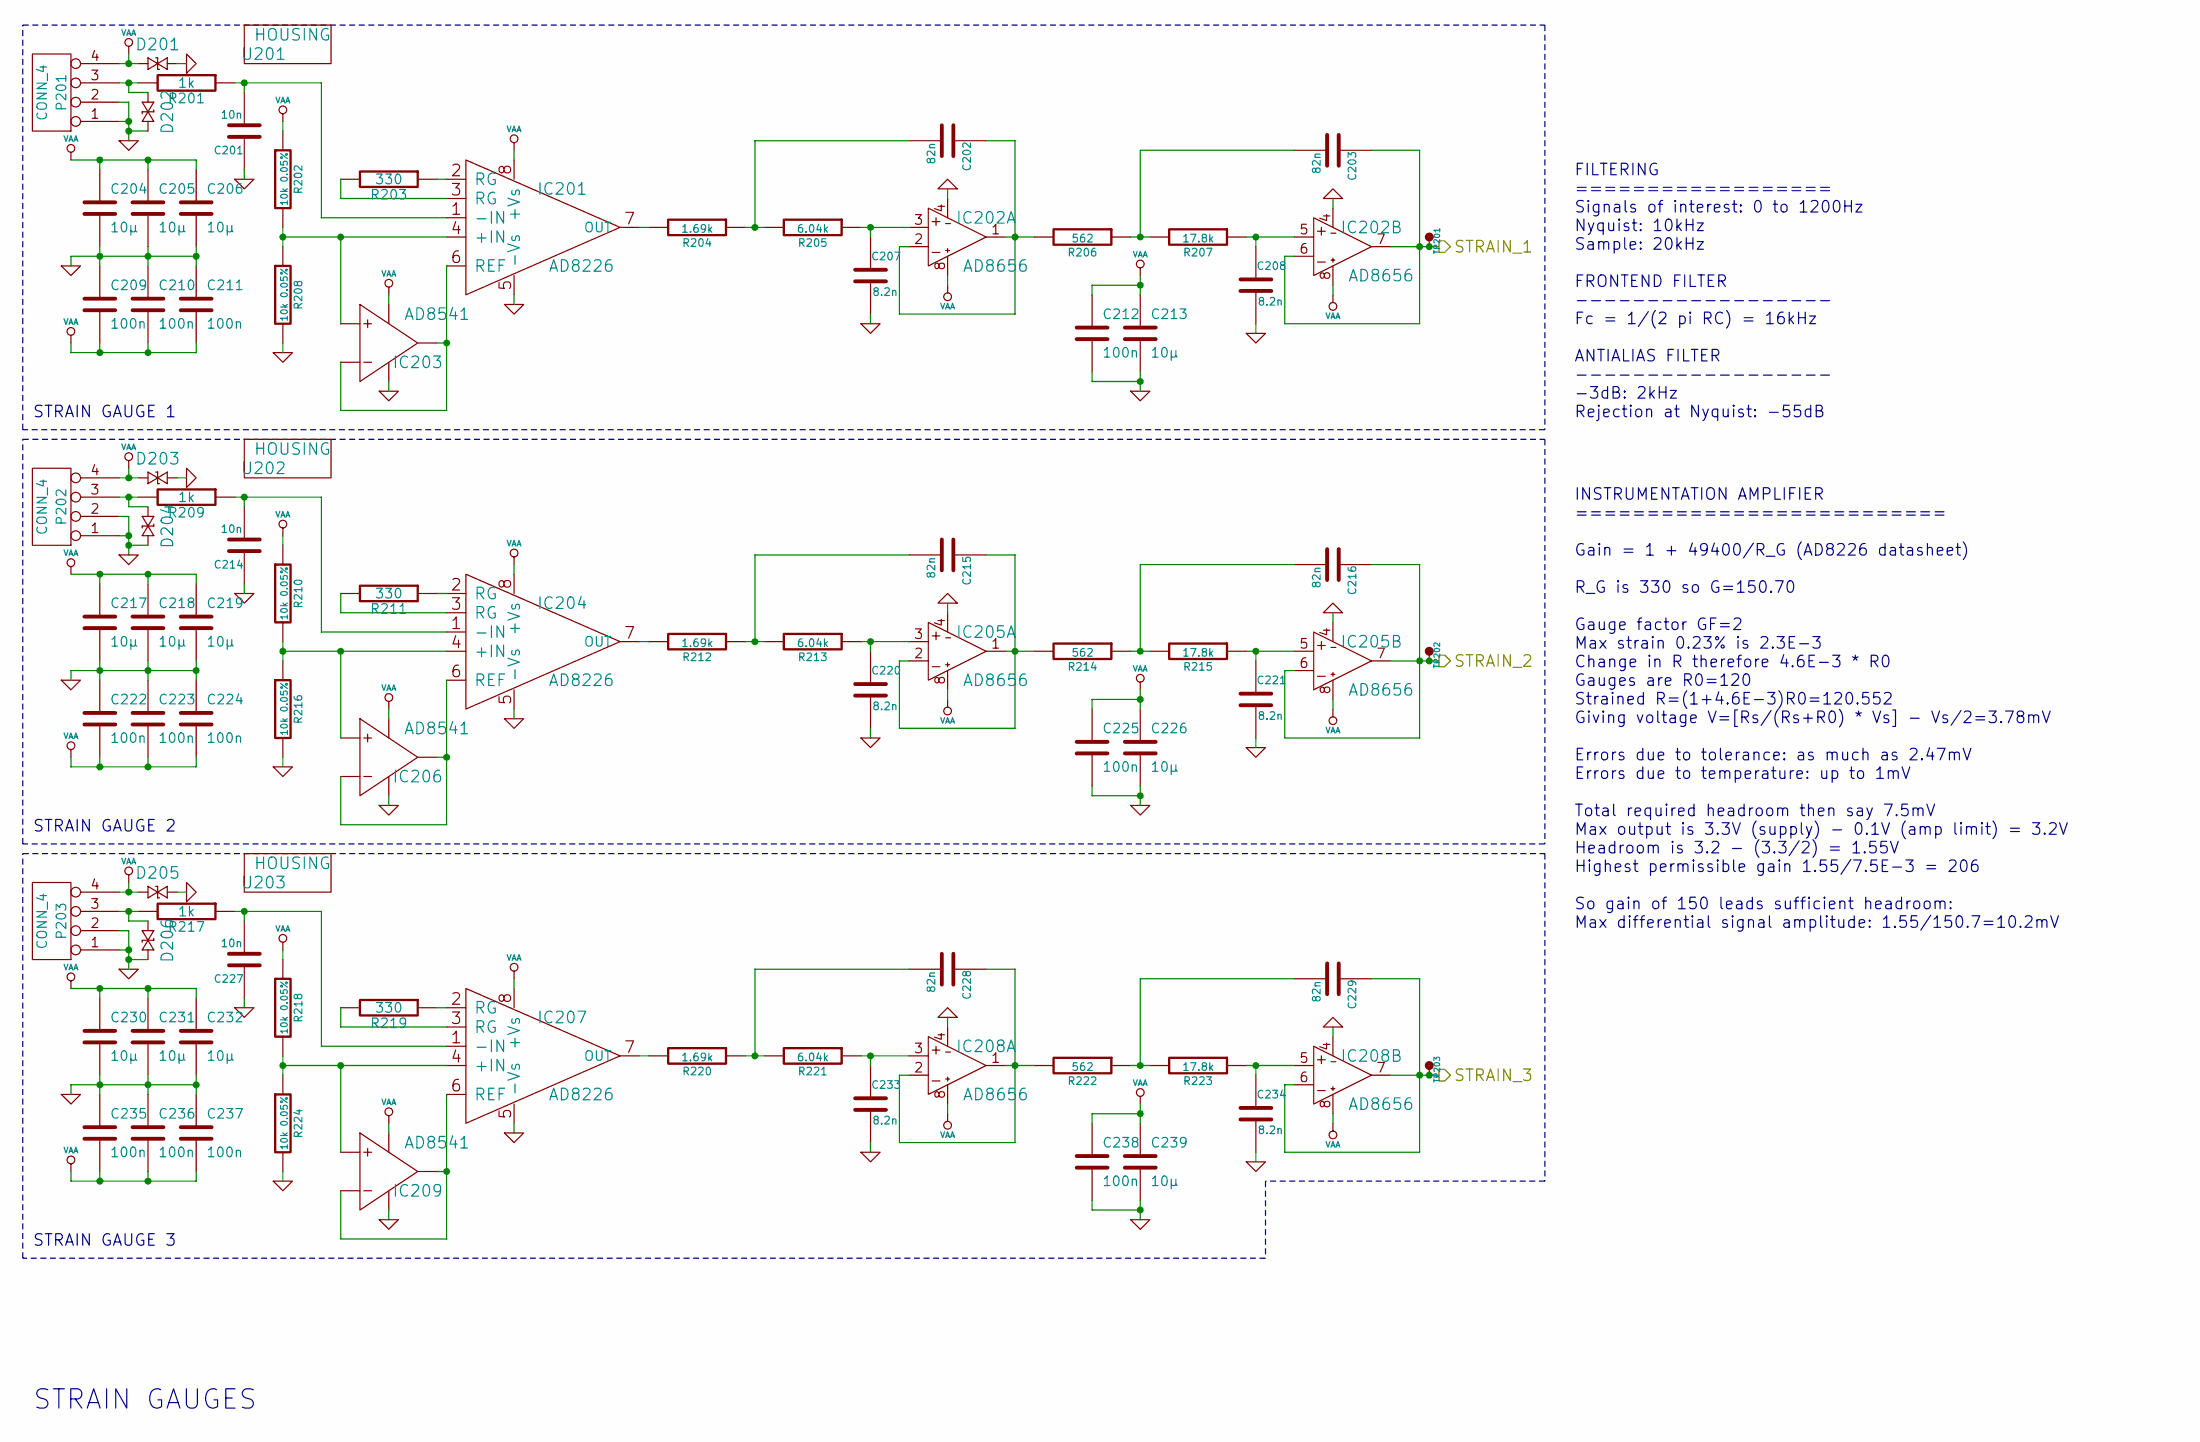
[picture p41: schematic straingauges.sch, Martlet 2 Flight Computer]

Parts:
C201, C214, C227: 10n; C0603; Farnell 2112704
C202, C203, C215, C216, C228, C229: 82n; C0603; Farnell 1865539
C204, C205, C206, C213, C217, C218, C219, C226, C230, C231, C232, C239: 10µ; C0603; Farnell 2211164
C207, C208, C220, C221, C233, C234: 8.2n; C0603; Farnell 2210859
C209, C210, C211, C212, C222, C223, C224, C225, C235, C236, C237, C238: 100n; C0603; Farnell 1759037
D201, D202, D203, D204, D205, D206: CGA0402MLC-12G; R0402; Farnell 2368169
IC201, IC204, IC207: AD8226; MSOP8; Farnell 1827359
IC202, IC205, IC208: AD8656; MSOP8; Farnell 1858055
IC203, IC206, IC209: AD8541; SC-70-5; Farnell 1837433
P201, P202, P203: CONN_4; S04B-PASK-2; Farnell 1830749
R201, R209, R217: 1k; R0603; Farnell 2116678
R202, R208, R210, R216, R218, R224: 10k 0.05%; R0603; Farnell 1877590
R203, R211, R219: 330; R0603; Farnell 1577599
R204, R212, R220: 1.69k; R0603; Farnell 2116702
R205, R213, R221: 6.04k; R0603; Farnell 2116761
R206, R214, R222: 562; R0603; Farnell 2116652
R207, R215, R223: 17.8k; R0603; Farnell 2116811
TP201, TP202, TP203: TESTPAD
U201, U202, U203: HOUSING; Farnell 1830729

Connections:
/StrainGauges/STRAIN_1: C203.1, IC202.6 (-IN), IC202.7 (OUT), TP201.1; also elsewhere on the board
/StrainGauges/STRAIN_2: C216.1, IC205.6 (-IN), IC205.7 (OUT), TP202.1; also elsewhere on the board
/StrainGauges/STRAIN_3: C229.1, IC208.6 (-IN), IC208.7 (OUT), TP203.1; also elsewhere on the board
GND: C201.1, C204.2, C205.2, C206.2, C207.2, C208.2, C209.1, C210.1, C211.1, C212.2, C213.2, C214.1, C217.2, C218.2, C219.2, C220.2, C221.2, C222.1, C223.1, C224.1, C225.2, C226.2, C227.1, C230.2, C231.2, C232.2, C233.2, C234.2, C235.1, C236.1, C237.1, C238.2, C239.2, D201.1, D202.1, D203.1, D204.1, D205.1, D206.1, IC201.5 (-Vs), IC202.4 (V-), IC203.2 (V-), IC204.5 (-Vs), IC205.4 (V-), IC206.2 (V-), IC207.5 (-Vs), IC208.4 (V-), IC209.2 (V-), P201.1, P201.2, P202.1, P202.2, P203.1, P203.2, R208.2, R216.2, R224.2; also elsewhere on the board
unnamed: C201.2, IC201.1 (-IN), R201.1
unnamed: C202.1, IC202.1 (OUT), IC202.2 (-IN), R206.2
unnamed: C202.2, R204.1, R205.2
unnamed: C203.2, R206.1, R207.2
unnamed: C207.1, IC202.3 (+IN), R205.1
unnamed: C208.1, IC202.5 (+IN), R207.1
unnamed: C214.2, IC204.1 (-IN), R209.1
unnamed: C215.1, IC205.1 (OUT), IC205.2 (-IN), R214.2
unnamed: C215.2, R212.1, R213.2
unnamed: C216.2, R214.1, R215.2
unnamed: C220.1, IC205.3 (+IN), R213.1
unnamed: C221.1, IC205.5 (+IN), R215.1
unnamed: C227.2, IC207.1 (-IN), R217.1
unnamed: C228.1, IC208.1 (OUT), IC208.2 (-IN), R222.2
unnamed: C228.2, R220.1, R221.2
unnamed: C229.2, R222.1, R223.2
unnamed: C233.1, IC208.3 (+IN), R221.1
unnamed: C234.1, IC208.5 (+IN), R223.1
unnamed: D202.2, P201.3, R201.2
unnamed: D204.2, P202.3, R209.2
unnamed: D206.2, P203.3, R217.2
unnamed: IC201.2 (RG), R203.1
unnamed: IC201.3 (RG), R203.2
unnamed: IC201.4 (+IN), IC203.3 (+), R202.2, R208.1
unnamed: IC201.6 (REF), IC203.1 (OUT), IC203.4 (-)
unnamed: IC201.7 (OUT), R204.2
unnamed: IC204.2 (RG), R211.1
unnamed: IC204.3 (RG), R211.2
unnamed: IC204.4 (+IN), IC206.3 (+), R210.2, R216.1
unnamed: IC204.6 (REF), IC206.1 (OUT), IC206.4 (-)
unnamed: IC204.7 (OUT), R212.2
unnamed: IC207.2 (RG), R219.1
unnamed: IC207.3 (RG), R219.2
unnamed: IC207.4 (+IN), IC209.3 (+), R218.2, R224.1
unnamed: IC207.6 (REF), IC209.1 (OUT), IC209.4 (-)
unnamed: IC207.7 (OUT), R220.2
VAA: C204.1, C205.1, C206.1, C209.2, C210.2, C211.2, C212.1, C213.1, C217.1, C218.1, C219.1, C222.2, C223.2, C224.2, C225.1, C226.1, C230.1, C231.1, C232.1, C235.2, C236.2, C237.2, C238.1, C239.1, D201.2, D203.2, D205.2, IC201.8 (+Vs), IC202.8 (V+), IC203.5 (V+), IC204.8 (+Vs), IC205.8 (V+), IC206.5 (V+), IC207.8 (+Vs), IC208.8 (V+), IC209.5 (V+), P201.4, P202.4, P203.4, R202.1, R210.1, R218.1; also elsewhere on the board

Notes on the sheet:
STRAIN GAUGE 1
FILTERING ================== Signals of interest: 0 to 1200Hz Nyquist: 10kHz Sample: 20kHz FRONTEND FILTER ------------------ Fc = 1/(2 pi RC) = 16kHz ANTIALIAS FILTER ------------------ -3dB: 2kHz Rejection at Nyquist: -55dB
STRAIN GAUGES
INSTRUMENTATION AMPLIFIER ========================== Gain = 1 + 49400/R_G (AD8226 datasheet) R_G is 330 so G=150.70 Gauge factor GF=2 Max strain 0.23% is 2.3E-3 Change in R therefore 4.6E-3 * R0 Gauges are R0=120 Strained R=(1+4.6E-3)R0=120.552 Giving voltage V=[Rs/(Rs+R0) * Vs] - Vs/2=3.78mV Error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
STRAIN GAUGE 2
STRAIN GAUGE 3

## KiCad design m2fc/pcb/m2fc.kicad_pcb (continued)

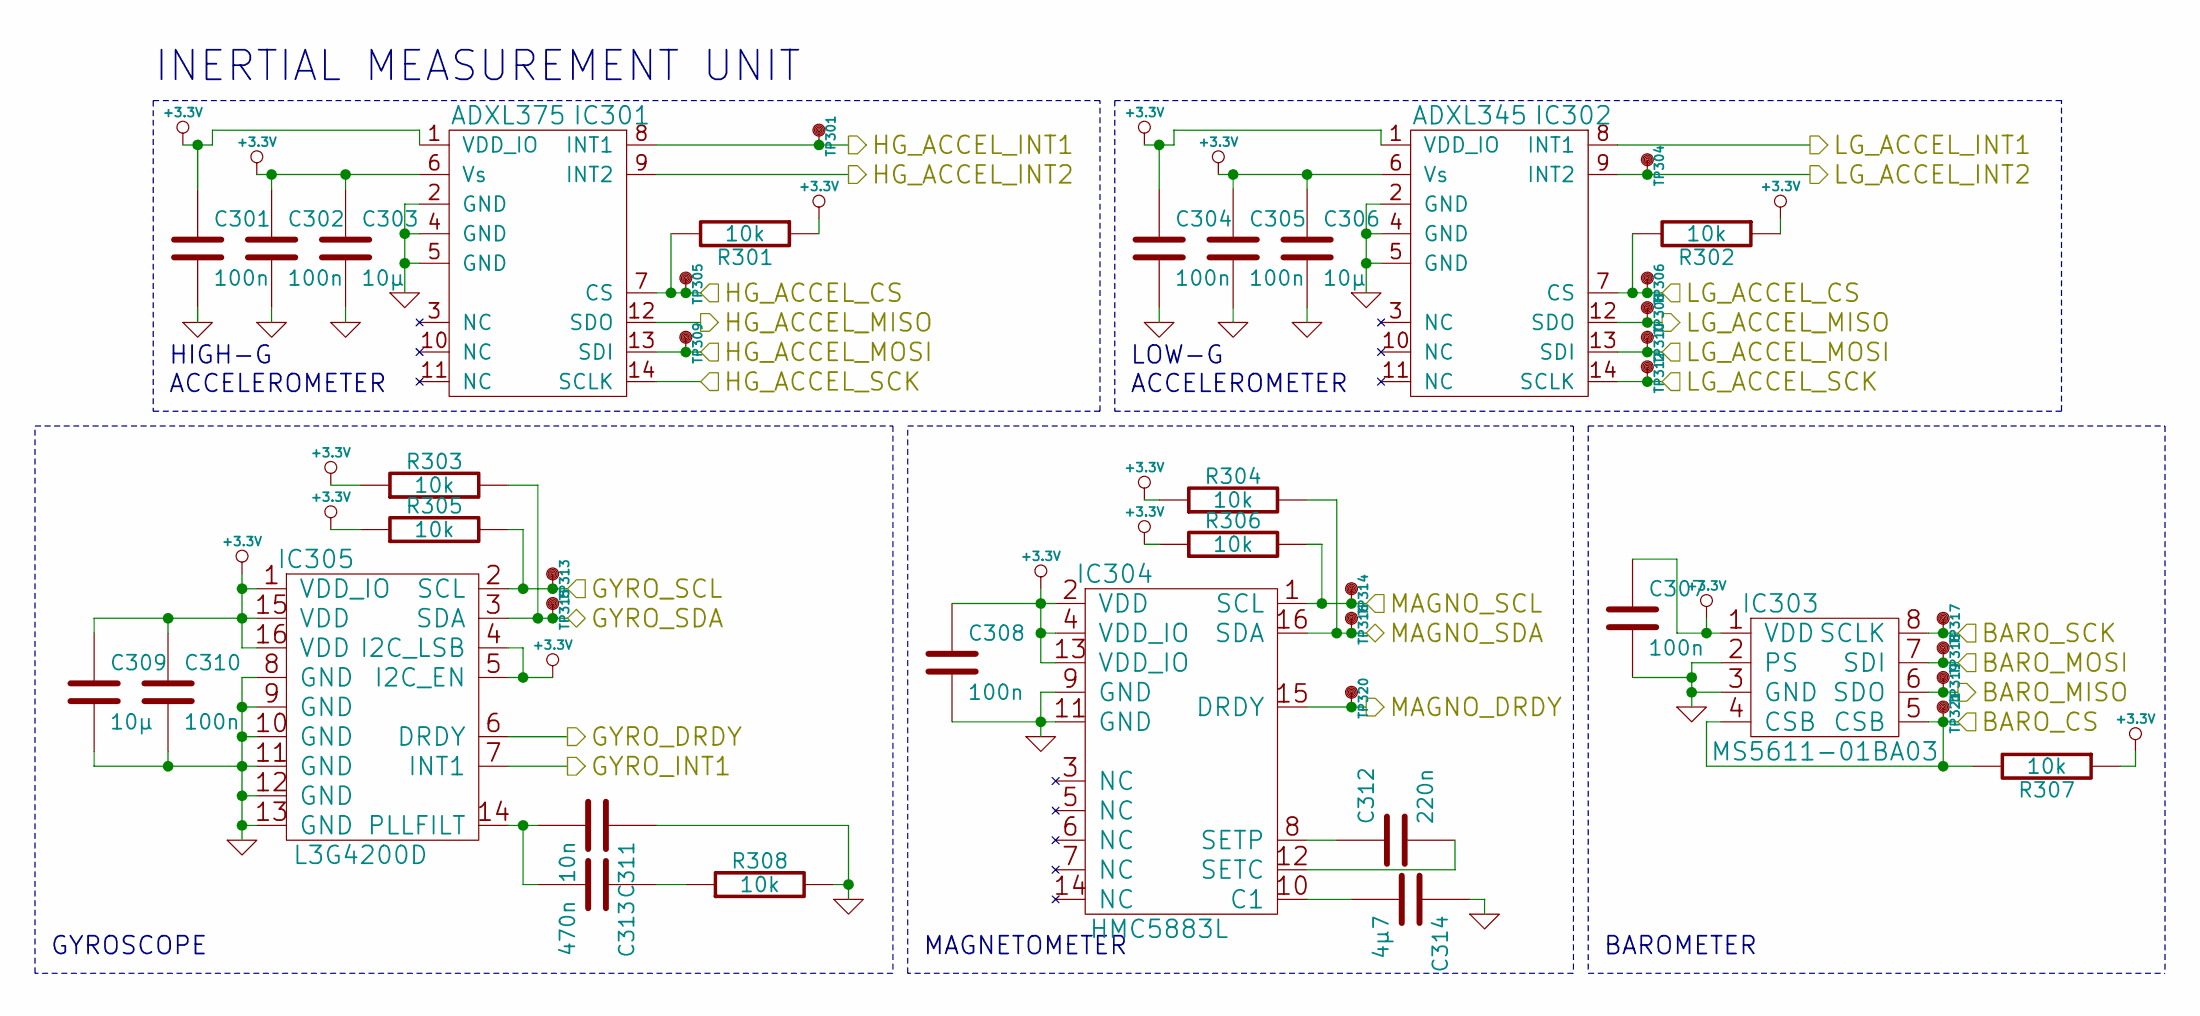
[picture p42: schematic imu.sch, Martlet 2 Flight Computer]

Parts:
C301, C302, C304, C305, C307, C308, C310: 100n; C0603; Farnell 1759037
C303, C306, C309: 10µ; C0603; Farnell 2211164
C311: 10n; C0603; Farnell 1833876
C312: 220n; C0603; Farnell 1833865
C313: 470n; C0603; Farnell 1867949
C314: 4µ7; C0603; Farnell 1833803
IC301: ADXL375; ADXL3x5; Farnell 2361527
IC302: ADXL345; ADXL3x5; Farnell 1853935
IC303: MS5611-01BA03; MS5611-01BA; Farnell 2362662
IC304: HMC5883L; Farnell 1971743
IC305: L3G4200D; Farnell 1872924
R301, R302, R303, R304, R305, R306, R307, R308: 10k; R0603; Farnell 2332016
TP301, TP304, TP305, TP306, TP308, TP309, TP310, TP312, TP313, TP314, TP315, TP316, TP317, TP318, TP319, TP320, TP321: TESTPAD

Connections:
+3.3V: C301.1, C302.1, C303.1, C304.1, C305.1, C306.1, C307.1, C308.1, C309.1, C310.1, IC301.1 (VDD_IO), IC301.6 (Vs), IC302.1 (VDD_IO), IC302.6 (Vs), IC303.1 (VDD), IC304.2 (VDD), IC304.4 (VDD_IO), IC304.13 (VDD_IO), IC305.1 (VDD_IO), IC305.4 (I2C_LSB), IC305.5 (I2C_EN), IC305.15 (VDD), IC305.16 (VDD), R301.1, R302.1, R303.1, R304.1, R305.1, R306.1, R307.1; also elsewhere on the board
/IMU/BARO_CS: IC303.4 (CSB), IC303.5 (CSB), R307.2, TP321.1; also elsewhere on the board
/IMU/BARO_MISO: IC303.6 (SDO), TP319.1; also elsewhere on the board
/IMU/BARO_MOSI: IC303.7 (SDI), TP318.1; also elsewhere on the board
/IMU/BARO_SCK: IC303.8 (SCLK), TP317.1; also elsewhere on the board
/IMU/GYRO_DRDY: IC305.6 (DRDY); also elsewhere on the board
/IMU/GYRO_INT1: IC305.7 (INT1); also elsewhere on the board
/IMU/GYRO_SCL: IC305.2 (SCL), R305.2, TP313.1; also elsewhere on the board
/IMU/GYRO_SDA: IC305.3 (SDA), R303.2, TP315.1; also elsewhere on the board
/IMU/HG_ACCEL_CS: IC301.7 (CS), R301.2, TP305.1; also elsewhere on the board
/IMU/HG_ACCEL_INT1: IC301.8 (INT1), TP301.1; also elsewhere on the board
/IMU/HG_ACCEL_INT2: IC301.9 (INT2); also elsewhere on the board
/IMU/HG_ACCEL_MISO: IC301.12 (SDO); also elsewhere on the board
/IMU/HG_ACCEL_MOSI: IC301.13 (SDI), TP309.1; also elsewhere on the board
/IMU/HG_ACCEL_SCK: IC301.14 (SCLK); also elsewhere on the board
/IMU/LG_ACCEL_CS: IC302.7 (CS), R302.2, TP306.1; also elsewhere on the board
/IMU/LG_ACCEL_INT1: IC302.8 (INT1); also elsewhere on the board
/IMU/LG_ACCEL_INT2: IC302.9 (INT2), TP304.1; also elsewhere on the board
/IMU/LG_ACCEL_MISO: IC302.12 (SDO), TP308.1; also elsewhere on the board
/IMU/LG_ACCEL_MOSI: IC302.13 (SDI), TP310.1; also elsewhere on the board
/IMU/LG_ACCEL_SCK: IC302.14 (SCLK), TP312.1; also elsewhere on the board
/IMU/MAGNO_DRDY: IC304.15 (DRDY), TP320.1; also elsewhere on the board
/IMU/MAGNO_SCL: IC304.1 (SCL), R306.2, TP314.1; also elsewhere on the board
/IMU/MAGNO_SDA: IC304.16 (SDA), R304.2, TP316.1; also elsewhere on the board
GND: C301.2, C302.2, C303.2, C304.2, C305.2, C306.2, C307.2, C308.2, C309.2, C310.2, C311.1, C314.1, IC301.2 (GND), IC301.4 (GND), IC301.5 (GND), IC302.2 (GND), IC302.4 (GND), IC302.5 (GND), IC303.2 (PS), IC303.3 (GND), IC304.9 (GND), IC304.11 (GND), IC305.8 (GND), IC305.9 (GND), IC305.10 (GND), IC305.11 (GND), IC305.12 (GND), IC305.13 (GND), R308.2; also elsewhere on the board
unnamed: C311.2, C313.2, IC305.14 (PLLFILT)
unnamed: C312.1, IC304.8 (SETP)
unnamed: C312.2, IC304.12 (SETC)
unnamed: C313.1, R308.1
unnamed: C314.2, IC304.10 (C1)

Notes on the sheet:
HIGH-G ACCELEROMETER
LOW-G ACCELEROMETER
GYROSCOPE
MAGNETOMETER
BAROMETER
INERTIAL MEASUREMENT UNIT

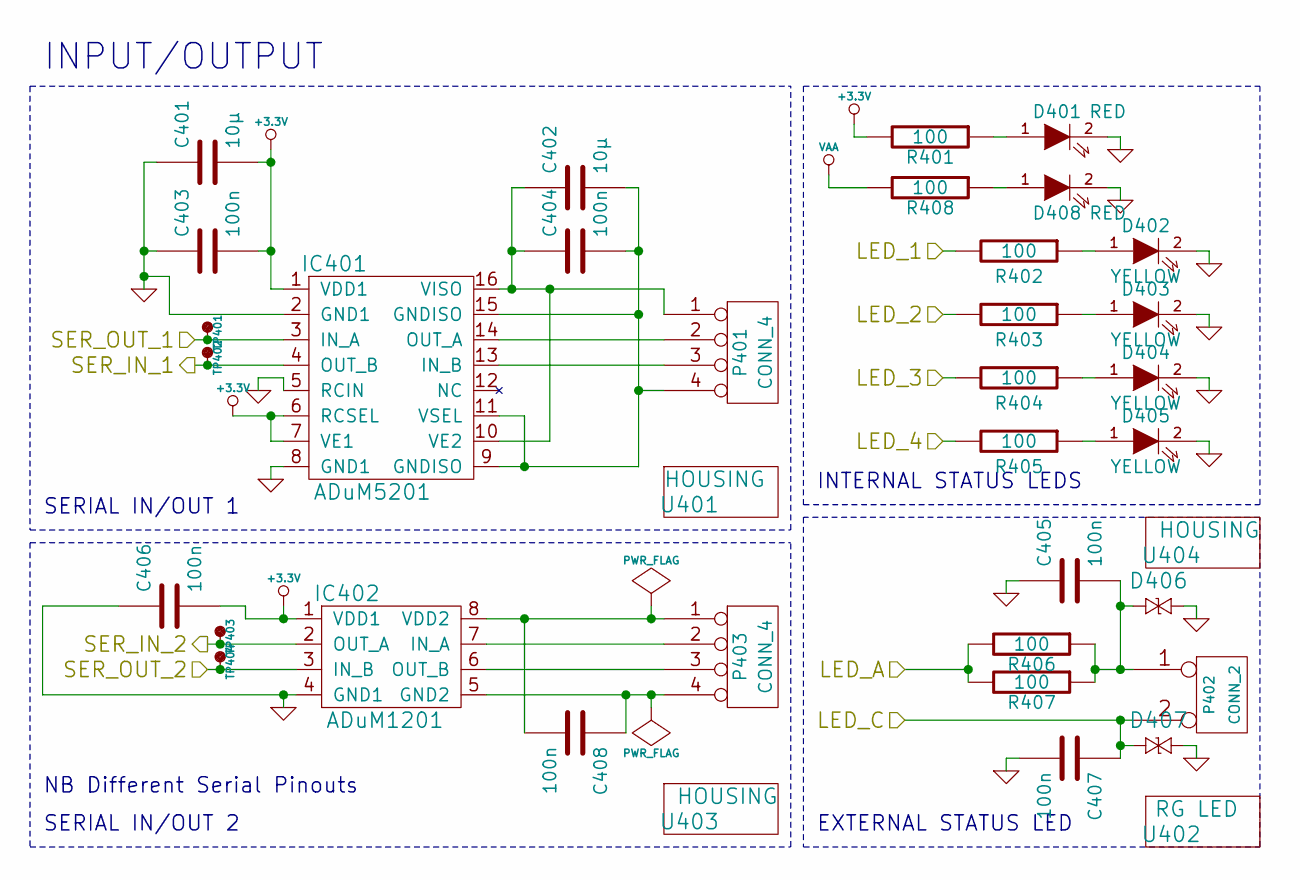
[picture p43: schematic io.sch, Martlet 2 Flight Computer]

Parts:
C401, C402: 10µ; C0603; Farnell 2211164
C403, C404, C405, C406, C407, C408: 100n; C0603; Farnell 1759037
D401, D408: RED; LED0603; Farnell 2290329
D402, D403, D404, D405: YELLOW; LED0603; Farnell 2290330
D406, D407: CGA0402MLC-12G; R0402; Farnell 2368169
IC401: ADuM5201; SOIC16; Farnell 2067773
IC402: ADuM1201; SOIC8; Farnell 1078200
P401, P403: CONN_4; S04B-PASK-2; Farnell 1830749
P402: CONN_2; S02B-PASK-2; Farnell 1830747
R401, R402, R403, R404, R405, R406, R407, R408: 100; R0603; Farnell 2331989
TP401, TP402, TP403, TP404: TESTPAD
U401, U403: HOUSING; Farnell 1830729
U402: RG LED; Farnell 1142488
U404: HOUSING; Farnell 1830726

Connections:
+3.3V: C401.2, C403.2, C406.2, IC401.1 (VDD1), IC401.6 (RCSEL), IC401.7 (VE1), IC402.1 (VDD1), R401.2; also elsewhere on the board
/IO/LED_1: R402.2; also elsewhere on the board
/IO/LED_2: R403.2; also elsewhere on the board
/IO/LED_3: R404.2; also elsewhere on the board
/IO/LED_4: R405.2; also elsewhere on the board
/IO/LED_A: R406.2, R407.2; also elsewhere on the board
/IO/LED_C: C407.1, D407.2, P402.2 (PM); also elsewhere on the board
/IO/SER_IN_1: IC401.4 (OUT_B), TP402.1; also elsewhere on the board
/IO/SER_IN_2: IC402.2 (OUT_A), TP403.1; also elsewhere on the board
/IO/SER_OUT_1: IC401.3 (IN_A), TP401.1; also elsewhere on the board
/IO/SER_OUT_2: IC402.3 (IN_B), TP404.1; also elsewhere on the board
GND: C401.1, C403.1, C405.1, C406.1, C407.2, D401.2 (K), D402.2 (K), D403.2 (K), D404.2 (K), D405.2 (K), D406.1, D407.1, D408.2 (K), IC401.2 (GND1), IC401.5 (RCIN), IC401.8 (GND1), IC402.4 (GND1); also elsewhere on the board
unnamed: C402.1, C404.1, IC401.10 (VE2), IC401.16 (VISO), P401.1
unnamed: C402.2, C404.2, IC401.9 (GNDISO), IC401.11 (VSEL), IC401.15 (GNDISO), P401.4
unnamed: C405.2, D406.2, P402.1, R406.1, R407.1
unnamed: C408.1, IC402.5 (GND2), P403.4
unnamed: C408.2, IC402.8 (VDD2), P403.1
unnamed: D401.1 (A), R401.1
unnamed: D402.1 (A), R402.1
unnamed: D403.1 (A), R403.1
unnamed: D404.1 (A), R404.1
unnamed: D405.1 (A), R405.1
unnamed: D408.1 (A), R408.1
unnamed: IC401.13 (IN_B), P401.3
unnamed: IC401.14 (OUT_A), P401.2
unnamed: IC402.6 (OUT_B), P403.3
unnamed: IC402.7 (IN_A), P403.2
VAA: R408.2; also elsewhere on the board

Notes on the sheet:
SERIAL IN/OUT 1
EXTERNAL STATUS LED
INTERNAL STATUS LEDS
INPUT/OUTPUT
SERIAL IN/OUT 2
NB Different Serial Pinouts

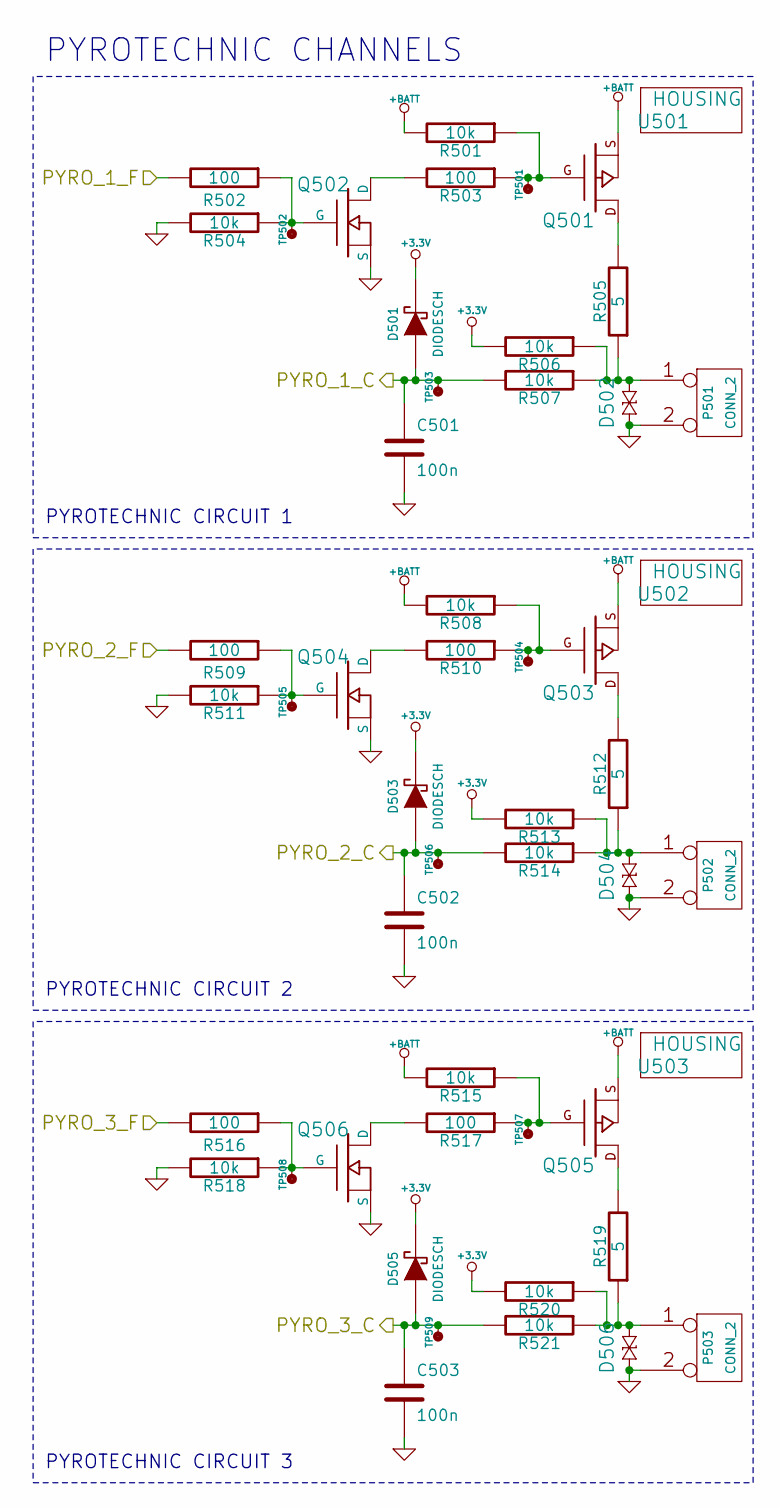
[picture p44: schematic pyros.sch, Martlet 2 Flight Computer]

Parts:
C501, C502, C503: 100n; C0603; Farnell 1759037
D501, D503, D505: DIODESCH; SOD323; Farnell 1349646
D502, D504, D506: CGA0402MLC-12G; R0402; Farnell 2368169
P501, P502, P503: CONN_2; S02B-PASK-2; Farnell 1830747
Q501, Q503, Q505: MOSFET_P; SOT-23-MOSFET; Farnell 1894738
Q502, Q504, Q506: MOSFET_N; SOT-23-MOSFET; Farnell 1510761
R501, R504, R506, R507, R508, R511, R513, R514, R515, R518, R520, R521: 10k; R0603; Farnell 2332016
R502, R503, R509, R510, R516, R517: 100; R0603; Farnell 2331989
R505, R512, R519: 5; PWR4318; Farnell 2328356
TP501, TP502, TP503, TP504, TP505, TP506, TP507, TP508, TP509: TESTPAD
U501, U502, U503: HOUSING; Farnell 1830726

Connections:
+3.3V: D501.2 (K), D503.2 (K), D505.2 (K), R506.2, R513.2, R520.2; also elsewhere on the board
+BATT: Q501.S, Q503.S, Q505.S, R501.2, R508.2, R515.2; also elsewhere on the board
/Pyros/PYRO_1_C: C501.1, D501.1 (A), R507.2, TP503.1; also elsewhere on the board
/Pyros/PYRO_1_F: R502.2; also elsewhere on the board
/Pyros/PYRO_2_C: C502.1, D503.1 (A), R514.2, TP506.1; also elsewhere on the board
/Pyros/PYRO_2_F: R509.2; also elsewhere on the board
/Pyros/PYRO_3_C: C503.1, D505.1 (A), R521.2, TP509.1; also elsewhere on the board
/Pyros/PYRO_3_F: R516.2; also elsewhere on the board
GND: C501.2, C502.2, C503.2, D502.2, D504.2, D506.2, P501.2 (PM), P502.2 (PM), P503.2 (PM), Q502.S, Q504.S, Q506.S, R504.2, R511.2, R518.2; also elsewhere on the board
unnamed: D502.1, P501.1, R505.1, R506.1, R507.1
unnamed: D504.1, P502.1, R512.1, R513.1, R514.1
unnamed: D506.1, P503.1, R519.1, R520.1, R521.1
unnamed: Q501.D, R505.2
unnamed: Q501.G, R501.1, R503.1, TP501.1
unnamed: Q502.D, R503.2
unnamed: Q502.G, R502.1, R504.1, TP502.1
unnamed: Q503.D, R512.2
unnamed: Q503.G, R508.1, R510.1, TP504.1
unnamed: Q504.D, R510.2
unnamed: Q504.G, R509.1, R511.1, TP505.1
unnamed: Q505.D, R519.2
unnamed: Q505.G, R515.1, R517.1, TP507.1
unnamed: Q506.D, R517.2
unnamed: Q506.G, R516.1, R518.1, TP508.1

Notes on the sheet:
PYROTECHNIC CIRCUIT 1
PYROTECHNIC CHANNELS
PYROTECHNIC CIRCUIT 2
PYROTECHNIC CIRCUIT 3

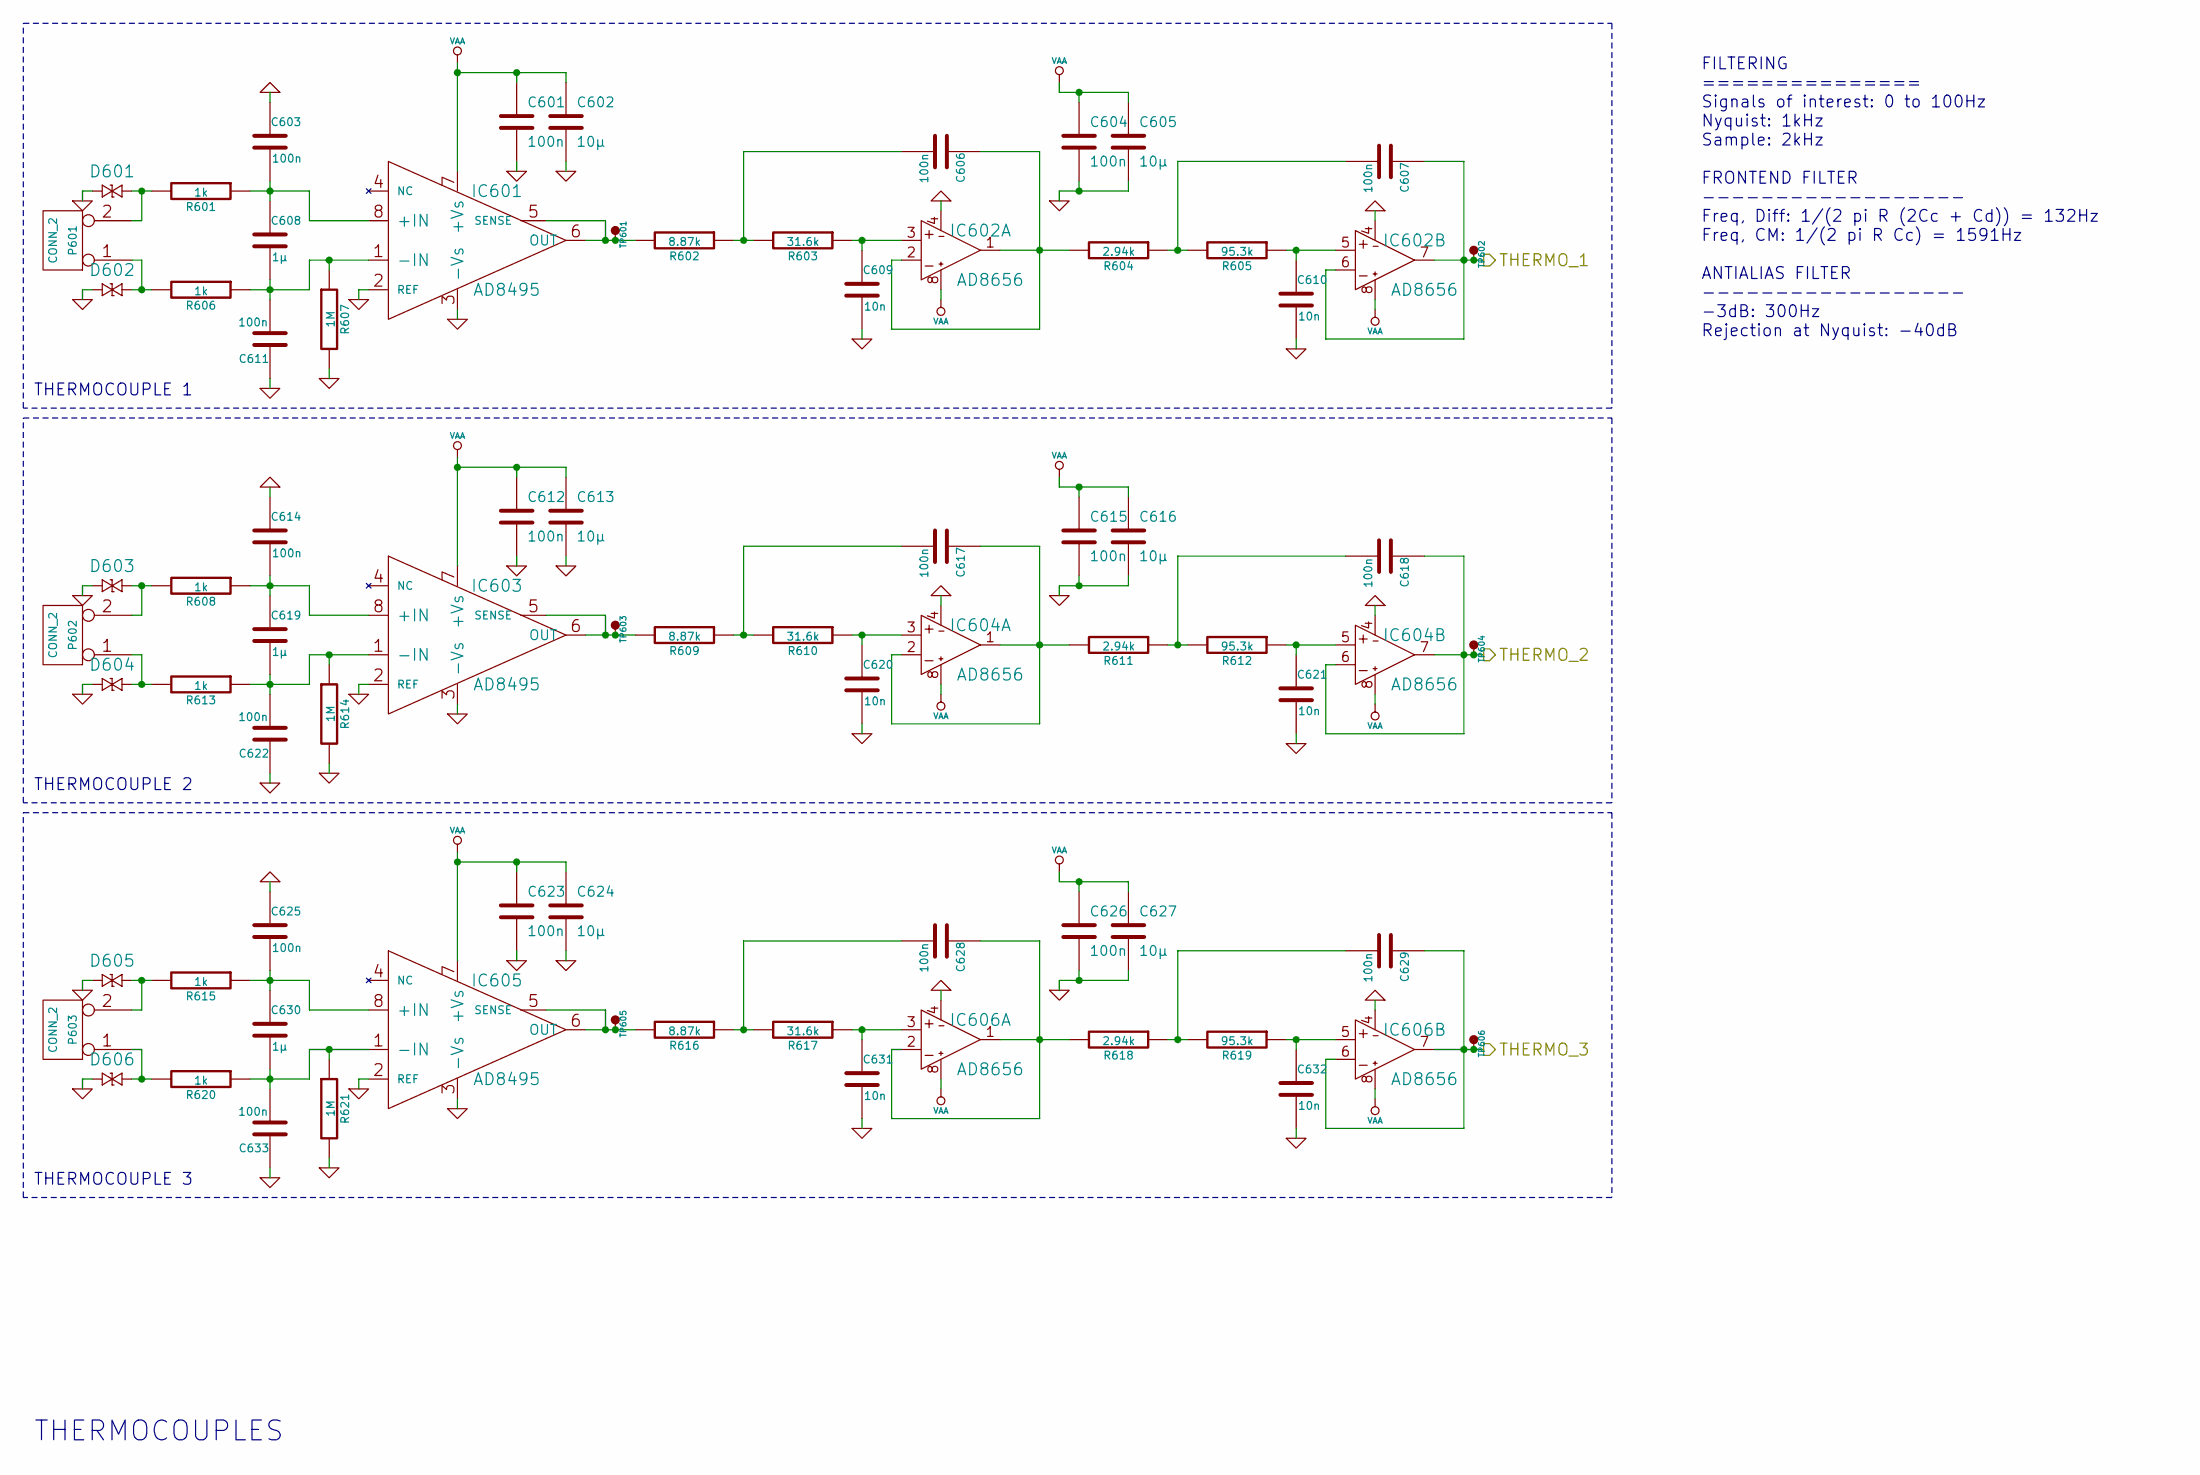
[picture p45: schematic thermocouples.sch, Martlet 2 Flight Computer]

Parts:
C601, C604, C612, C615, C623, C626: 100n; C0603; Farnell 1759037
C602, C605, C613, C616, C624, C627: 10µ; C0603; Farnell 2211164
C603, C606, C607, C611, C614, C617, C618, C622, C625, C628, C629, C633: 100n; C1206; Farnell 2211074
C608, C619, C630: 1µ; C0603; Farnell 2346895
C609, C610, C620, C621, C631, C632: 10n; C0603; Farnell 2112704
D601, D602, D603, D604, D605, D606: CGA0402MLC-12G; R0402; Farnell 2368169
IC601, IC603, IC605: AD8495; MSOP8; Farnell 2067807
IC602, IC604, IC606: AD8656; MSOP8; Farnell 1858055
P601, P602, P603: CONN_2; S02B-PASK-2; Farnell 1830747
R601, R606, R608, R613, R615, R620: 1k; R0603; Farnell 2116678
R602, R609, R616: 8.87k; R0603; Farnell 2116779
R603, R610, R617: 31.6k; R0603; Farnell 2116838
R604, R611, R618: 2.94k; R0603; Farnell 2116727
R605, R612, R619: 95.3k; R0603; Farnell 2116889
R607, R614, R621: 1M; R0603; Farnell 2321755
TP601, TP602, TP603, TP604, TP605, TP606: TESTPAD

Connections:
/Thermocouples/THERMO_1: C607.1, IC602.6 (-IN), IC602.7 (OUT), TP602.1; also elsewhere on the board
/Thermocouples/THERMO_2: C618.1, IC604.6 (-IN), IC604.7 (OUT), TP604.1; also elsewhere on the board
/Thermocouples/THERMO_3: C629.1, IC606.6 (-IN), IC606.7 (OUT), TP606.1; also elsewhere on the board
GND: C601.2, C602.2, C603.1, C604.2, C605.2, C609.2, C610.2, C611.1, C612.2, C613.2, C614.1, C615.2, C616.2, C620.2, C621.2, C622.1, C623.2, C624.2, C625.1, C626.2, C627.2, C631.2, C632.2, C633.1, D601.2, D602.2, D603.2, D604.2, D605.2, D606.2, IC601.2 (REF), IC601.3 (-Vs), IC602.4 (V-), IC603.2 (REF), IC603.3 (-Vs), IC604.4 (V-), IC605.2 (REF), IC605.3 (-Vs), IC606.4 (V-), R607.2, R614.2, R621.2; also elsewhere on the board
unnamed: C603.2, C608.1, IC601.8 (+IN), R601.1
unnamed: C606.1, IC602.1 (OUT), IC602.2 (-IN), R604.2
unnamed: C606.2, R602.1, R603.2
unnamed: C607.2, R604.1, R605.2
unnamed: C608.2, C611.2, IC601.1 (-IN), R606.1, R607.1
unnamed: C609.1, IC602.3 (+IN), R603.1
unnamed: C610.1, IC602.5 (+IN), R605.1
unnamed: C614.2, C619.1, IC603.8 (+IN), R608.1
unnamed: C617.1, IC604.1 (OUT), IC604.2 (-IN), R611.2
unnamed: C617.2, R609.1, R610.2
unnamed: C618.2, R611.1, R612.2
unnamed: C619.2, C622.2, IC603.1 (-IN), R613.1, R614.1
unnamed: C620.1, IC604.3 (+IN), R610.1
unnamed: C621.1, IC604.5 (+IN), R612.1
unnamed: C625.2, C630.1, IC605.8 (+IN), R615.1
unnamed: C628.1, IC606.1 (OUT), IC606.2 (-IN), R618.2
unnamed: C628.2, R616.1, R617.2
unnamed: C629.2, R618.1, R619.2
unnamed: C630.2, C633.2, IC605.1 (-IN), R620.1, R621.1
unnamed: C631.1, IC606.3 (+IN), R617.1
unnamed: C632.1, IC606.5 (+IN), R619.1
unnamed: D601.1, P601.2 (PM), R601.2
unnamed: D602.1, P601.1, R606.2
unnamed: D603.1, P602.2 (PM), R608.2
unnamed: D604.1, P602.1, R613.2
unnamed: D605.1, P603.2 (PM), R615.2
unnamed: D606.1, P603.1, R620.2
unnamed: IC601.5 (SENSE), IC601.6 (OUT), R602.2, TP601.1
unnamed: IC603.5 (SENSE), IC603.6 (OUT), R609.2, TP603.1
unnamed: IC605.5 (SENSE), IC605.6 (OUT), R616.2, TP605.1
VAA: C601.1, C602.1, C604.1, C605.1, C612.1, C613.1, C615.1, C616.1, C623.1, C624.1, C626.1, C627.1, IC601.7 (+Vs), IC602.8 (V+), IC603.7 (+Vs), IC604.8 (V+), IC605.7 (+Vs), IC606.8 (V+); also elsewhere on the board

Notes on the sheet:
FILTERING =============== Signals of interest: 0 to 100Hz Nyquist: 1kHz Sample: 2kHz FRONTEND FILTER ------------------ Freq, Diff: 1/(2 pi R (2Cc + Cd)) = 132Hz Freq, CM: 1/(2 pi R Cc) = 1591Hz ANTIALIAS FILTER ------------------ -3dB: 300Hz Rejection at Nyquist: -40dB
THERMOCOUPLES
THERMOCOUPLE 1
THERMOCOUPLE 2
THERMOCOUPLE 3

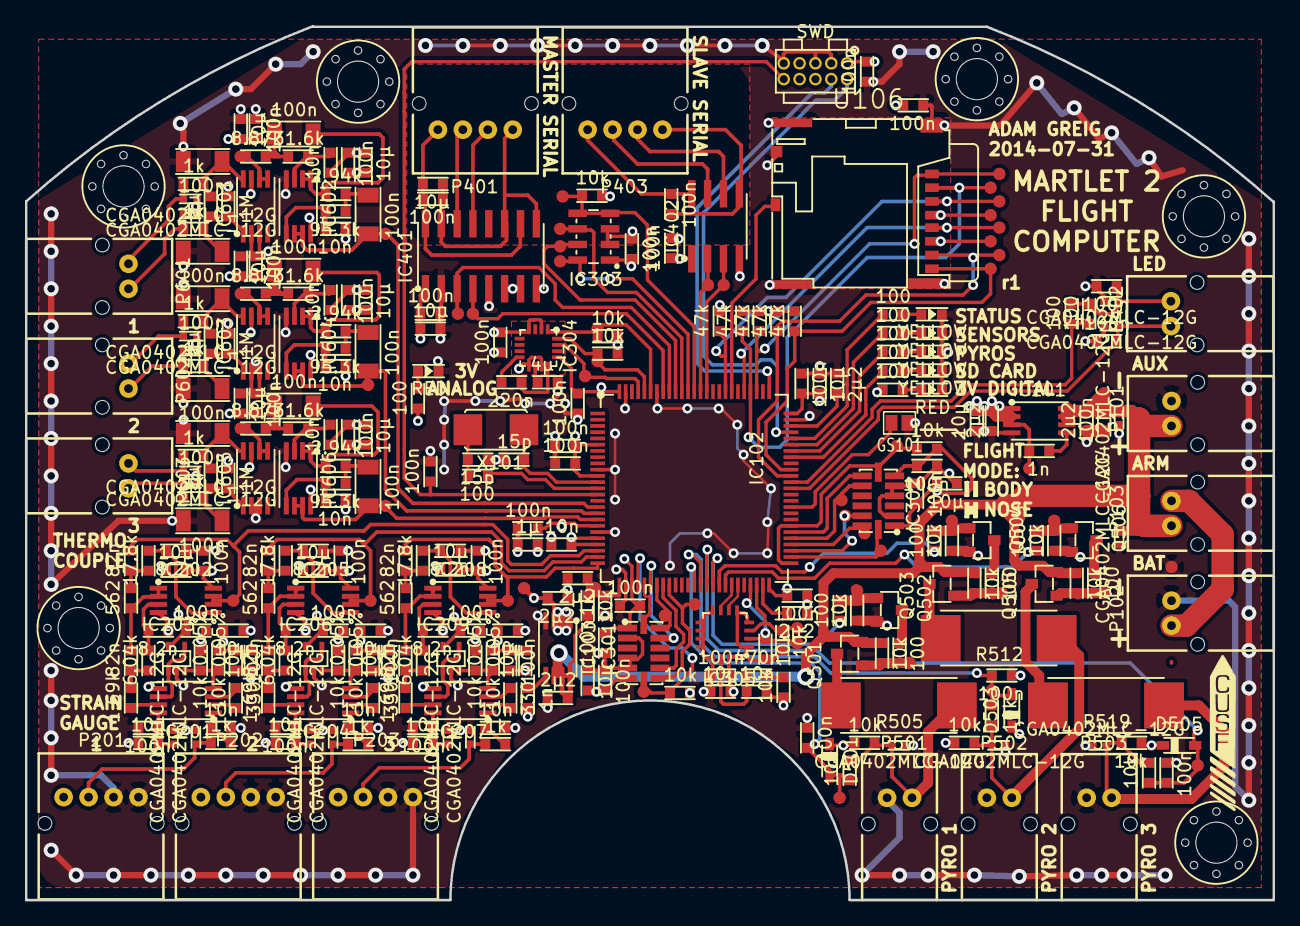
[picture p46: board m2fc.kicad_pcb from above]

Board: 4 copper layers, 100.0 x 70.0 mm, 351 parts (1 on the bottom side), 170 nets.

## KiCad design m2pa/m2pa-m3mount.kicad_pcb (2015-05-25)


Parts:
C1: 10p; C0402; Farnell 1327593
C2, C7: 20p; C0402; Farnell 1885343
C3: 100p; C0402; Farnell 1327627
C4: 10n; C0603; Farnell 2112704
C5: 6p2; C0402; Farnell 1885324
C6: 10µ; C1206; Farnell 2211068
D1, D2, D3: CGA0402MLC-12G; R0402; Farnell 2368169
IC1: ADL5324; SOT89-3; Farnell 2099794
L1: 1n6; L0603; Farnell 2285968
L2: 120n; L0603; Farnell 2285957
L3: 5n6; L0402; Farnell 2285660
P1: CONN_01X02; S02B-PASK-2; Farnell 1830747
P2, P3: SMA; SMA-142-0701-801; Farnell 1608592
R1: 2; R0402; Farnell 2141424

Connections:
+5V: C3.1, C4.1, C6.1, D3.1, L2.2, P1.2
GND: C2.1, C3.2, C4.2, C5.1, C6.2, D1.2, D2.2, D3.2, IC1.2 (GND), P1.1, P2.2 (GND), P2.3 (GND), P2.4 (GND), P2.5 (GND), P3.2 (GND), P3.3 (GND), P3.4 (GND), P3.5 (GND)
unnamed: C1.1, C2.2, L1.2
unnamed: C1.2, D1.1, P2.1 (RF)
unnamed: C5.2, C7.1, L3.1
unnamed: C7.2, D2.1, P3.1 (RF)
unnamed: IC1.1 (RFIN), R1.1
unnamed: IC1.3 (RFOUT), L2.1, L3.2
unnamed: L1.1, R1.2

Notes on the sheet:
COMPONENT PLACEMENT CRITICAL REFER TO ADL5324 DATASHEET FIGURE 41


Board: 2 copper layers, 47.0 x 28.0 mm, 22 parts (0 on the bottom side), 9 nets.

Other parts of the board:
M3_MOUNT, M3_MOUNT#2, M3_MOUNT#3, M3_MOUNT#4: VAL**; M3_MOUNT

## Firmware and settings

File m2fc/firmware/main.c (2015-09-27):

/*
 * M2FC
 * 2014 Adam Greig, Cambridge University Spaceflight
 */

#include <stdio.h>
#include <string.h>

#include "ch.h"
#include "hal.h"

#include "ff.h"

#include "ms5611.h"
#include "adxl3x5.h"
#include "config.h"
#include "pyro.h"
#include "datalogging.h"
#include "m2fc_shell.h"
#include "mission.h"
#include "state_estimation.h"
#include "analogue.h"
#include "l3g4200d.h"
#include "hmc5883l.h"
#include "dma_mutexes.h"
#include "m2serial.h"
#include "m2status.h"

/* Create working areas for all threads */
/* TODO: Move some stacks to CCM where possible (no DMA use). */
static WORKING_AREA(waMS5611, 768);
static WORKING_AREA(waADXL345, 512);
static WORKING_AREA(waADXL375, 512);
static WORKING_AREA(waMission, 1024);
static WORKING_AREA(waThreadHB, 128);
static WORKING_AREA(waDatalogging, 2048);
static WORKING_AREA(waConfig, 8192);
static WORKING_AREA(waPyros, 128);
/*static WORKING_AREA(waThreadSBP, 1024);*/
static WORKING_AREA(waAnalogue, 512);
static WORKING_AREA(waHMC5883L, 512);
static WORKING_AREA(waL3G4200D, 1024);
static WORKING_AREA(waM2Serial, 1024);
static WORKING_AREA(waM2Status, 1024);

/*
 * Heatbeat thread.
 * This thread flashes the everything-is-OK LED once a second,
 * and keeps resetting the watchdog timer for us.
 */
static msg_t ThreadHeartbeat(void *arg) {
    uint8_t mystatus;
    (void)arg;
    chRegSetThreadName("Heartbeat");

    while(TRUE) {
        /* Set the STATUS onboard LED */
        palSetPad(GPIOA, GPIOA_LED_STATUS);
        /* Set external LED */
        if(LocalStatus == &M2FCBodyStatus) {
            mystatus = M2FCBodyStatus.m2fcbody;
        } else if(LocalStatus == &M2FCNoseStatus) {
            mystatus = M2FCNoseStatus.m2fcnose;
        }
        if(mystatus == STATUS_OK) {
            /* Set the GREEN external LED */
            palClearPad(GPIOC, GPIOC_LED_C);
            palSetPad(GPIOC, GPIOC_LED_A);
        } else {
            /* Set the RED external LED */
            palSetPad(GPIOC, GPIOC_LED_C);
            palClearPad(GPIOC, GPIOC_LED_A);
        }
        /* Flash them briefly */
        chThdSleepMilliseconds(20);

        /* Turn LEDs off */
        palClearPad(GPIOA, GPIOA_LED_STATUS);
        palClearPad(GPIOC, GPIOC_LED_C);
        palClearPad(GPIOC, GPIOC_LED_A);

        /* Clear watchdog timer */
        IWDG->KR = 0xAAAA;
        chThdSleepMilliseconds(480);
    }

    return RDY_OK;
}

/*
 * Set up pin change interrupts for the various sensors that react to them.
 */
static const EXTConfig extcfg = {{
    {EXT_CH_MODE_AUTOSTART | EXT_CH_MODE_RISING_EDGE | EXT_MODE_GPIOE,
        hmc5883l_wakeup},         /* Pin 0 - PE0 is the magnetometer DRDY */
    {EXT_CH_MODE_DISABLED, NULL}, /* Pin 1 */
    {EXT_CH_MODE_DISABLED, NULL}, /* Pin 2 */
    {EXT_CH_MODE_DISABLED, NULL}, /* Pin 3 */
    {EXT_CH_MODE_DISABLED, NULL}, /* Pin 4 */
    {EXT_CH_MODE_AUTOSTART | EXT_CH_MODE_RISING_EDGE | EXT_MODE_GPIOC,
        adxl375_wakeup},          /* Pin 5 - PC5 is the HG accel INT1 */
    {EXT_CH_MODE_DISABLED, NULL}, /* Pin 6 */
    {EXT_CH_MODE_DISABLED, NULL}, /* Pin 7 */
    {EXT_CH_MODE_DISABLED, NULL}, /* Pin 8 */
    {EXT_CH_MODE_AUTOSTART | EXT_CH_MODE_RISING_EDGE | EXT_MODE_GPIOD,
        adxl345_wakeup},          /* Pin 9 - PD9 is the LG accel INT1 */
    {EXT_CH_MODE_DISABLED, NULL}, /* Pin 10 */
    {EXT_CH_MODE_DISABLED, NULL}, /* Pin 11 */
    {EXT_CH_MODE_DISABLED, NULL}, /* Pin 12 */
    {EXT_CH_MODE_DISABLED, NULL}, /* Pin 13 */
    {EXT_CH_MODE_AUTOSTART | EXT_CH_MODE_RISING_EDGE | EXT_MODE_GPIOE,
        l3g4200d_wakeup},         /* Pin 14 - PE14 is the gyro DRDY */
    {EXT_CH_MODE_DISABLED, NULL}, /* Pin 15 */
    {EXT_CH_MODE_DISABLED, NULL}, /* 16 - PVD */
    {EXT_CH_MODE_DISABLED, NULL}, /* 17 - RTC Alarm */
    {EXT_CH_MODE_DISABLED, NULL}, /* 18 - USB OTG FS Wakeup */
    {EXT_CH_MODE_DISABLED, NULL}, /* 19 - Ethernet Wakeup */
    {EXT_CH_MODE_DISABLED, NULL}, /* 20 - USB OTG HS Wakeup */
    {EXT_CH_MODE_DISABLED, NULL}, /* 21 - RTC Tamper/Timestamp */
    {EXT_CH_MODE_DISABLED, NULL}  /* 22 - RTC Wakeup */
}};

/*
 * M2FC Main Thread.
 * Starts all the other threads then puts itself to sleep.
 */
int main(void) {
    halInit();
    chSysInit();
    chRegSetThreadName("Main");

    /* Start the heartbeat thread so it will be resetting the watchdog. */
    chThdCreateStatic(waThreadHB, sizeof(waThreadHB), LOWPRIO,
                      ThreadHeartbeat, NULL);

    /* Configure and enable the watchdog timer, stopped in debug halt. */
    DBGMCU->APB1FZ |= DBGMCU_APB1_FZ_DBG_IWDG_STOP;
    IWDG->KR = 0x5555;
    IWDG->PR = 3;
    IWDG->KR = 0xCCCC;

    /* Various module initialisation */
    state_estimation_init();
    dma_mutexes_init();

    /* Read config from SD card and wait for completion. */
    Thread* cfg_tp = chThdCreateStatic(waConfig, sizeof(waConfig),
                                       NORMALPRIO, config_thread, NULL);
    while(cfg_tp->p_state != THD_STATE_FINAL) chThdSleepMilliseconds(10);
    if(conf.location == CFG_M2FC_BODY)
        LocalStatus = &M2FCBodyStatus;
    else if(conf.location == CFG_M2FC_NOSE)
        LocalStatus = &M2FCNoseStatus;
    if(conf.config_loaded)
        m2status_config_status(STATUS_OK);
    else
        m2status_config_status(STATUS_ERR);

    /* Activate the EXTI pin change interrupts */
    extStart(&EXTD1, &extcfg);

    /* Start module threads */
    m2serial_shell = m2fc_shell_run;
    M2SerialSD = &SD1;
    sdStart(M2SerialSD, NULL);
    chThdCreateStatic(waM2Serial, sizeof(waM2Serial), HIGHPRIO,
                      m2serial_thread, NULL);

    chThdCreateStatic(waM2Status, sizeof(waM2Status), HIGHPRIO,
                      m2status_thread, NULL);

    chThdCreateStatic(waDatalogging, sizeof(waDatalogging), HIGHPRIO,
                      datalogging_thread, NULL);

    chThdCreateStatic(waMission, sizeof(waMission), NORMALPRIO,
                      mission_thread, NULL);

    chThdCreateStatic(waMS5611, sizeof(waMS5611), NORMALPRIO,
                      ms5611_thread, NULL);

    chThdCreateStatic(waADXL345, sizeof(waADXL345), NORMALPRIO,
                      adxl345_thread, NULL);

    chThdCreateStatic(waADXL375, sizeof(waADXL375), NORMALPRIO,
                      adxl375_thread, NULL);

    chThdCreateStatic(waPyros, sizeof(waPyros), NORMALPRIO,
                      pyro_continuity_thread, NULL);

    if(conf.use_gyro) {
        chThdCreateStatic(waL3G4200D, sizeof(waL3G4200D), NORMALPRIO,
                          l3g4200d_thread, NULL);
    } else {
        m2status_gyro_status(STATUS_OK);
    }

    if(conf.use_magno) {
        chThdCreateStatic(waHMC5883L, sizeof(waHMC5883L), NORMALPRIO,
                          hmc5883l_thread, NULL);
    } else {
        m2status_magno_status(STATUS_OK);
    }

    if(conf.use_adc) {
        chThdCreateStatic(waAnalogue, sizeof(waAnalogue), NORMALPRIO,
                          analogue_thread, NULL);
    } else {
        m2status_adc_status(STATUS_OK);
    }

    /* Let the main thread idle now. */
    chThdSetPriority(LOWPRIO);
    chThdSleep(TIME_INFINITE);

    return 0;
}

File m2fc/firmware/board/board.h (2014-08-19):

/*
 * M2FC ChibiOS Board definition file.
*/

#ifndef _BOARD_H_
#define _BOARD_H_

/*
 * Board identifier.
 */
#define BOARD_M2FC
#define BOARD_NAME                  "M2FC"


/*
 * Board oscillators-related settings.
 */
#if !defined(STM32_LSECLK)
#define STM32_LSECLK                0
#endif

#if !defined(STM32_HSECLK)
#define STM32_HSECLK                8000000
#endif

/*
 * Board voltages.
 * Required for performance limits calculation.
 */
#define STM32_VDD                   330

/*
 * MCU type as defined in the ST header.
 */
#define STM32F40_41xxx

/*
 * IO pins assignments.
 */
#define GPIOA_STRAIN_1              0
#define GPIOA_STRAIN_2              1
#define GPIOA_STRAIN_3              2
#define GPIOA_BAT_MON               3
#define GPIOA_HG_ACCEL_CS           4
#define GPIOA_HG_ACCEL_SCK          5
#define GPIOA_HG_ACCEL_MISO         6
#define GPIOA_HG_ACCEL_MOSI         7
#define GPIOA_PIN8                  8
#define GPIOA_LED_SDCARD            9
#define GPIOA_LED_PYROS             10
#define GPIOA_LED_SENSORS           11
#define GPIOA_LED_STATUS            12
#define GPIOA_SWDIO                 13
#define GPIOA_SWCLK                 14
#define GPIOA_PIN15                 15

#define GPIOB_PIN0                  0
#define GPIOB_PIN1                  1
#define GPIOB_PIN2                  2
#define GPIOB_BARO_SCK              3
#define GPIOB_BARO_MISO             4
#define GPIOB_BARO_MOSI             5
#define GPIOB_SER_OUT_1             6
#define GPIOB_SER_IN_1              7
#define GPIOB_MAGNO_SCL             8
#define GPIOB_MAGNO_SDA             9
#define GPIOB_GYRO_SCL              10
#define GPIOB_GYRO_SDA              11
#define GPIOB_LG_ACCEL_CS           12
#define GPIOB_LG_ACCEL_SCK          13
#define GPIOB_LG_ACCEL_MISO         14
#define GPIOB_LG_ACCEL_MOSI         15

#define GPIOC_PIN0                  0
#define GPIOC_THERMO_1              1
#define GPIOC_THERMO_2              2
#define GPIOC_THERMO_3              3
#define GPIOC_HG_ACCEL_INT2         4
#define GPIOC_HG_ACCEL_INT1         5
#define GPIOC_LED_C                 6
#define GPIOC_LED_A                 7
#define GPIOC_SD_DAT0               8
#define GPIOC_SD_DAT1               9
#define GPIOC_SD_DAT2               10
#define GPIOC_SD_DAT3               11
#define GPIOC_SD_CLK                12
#define GPIOC_PIN13                 13
#define GPIOC_PIN14                 14
#define GPIOC_PIN15                 15

#define GPIOD_PIN0                  0
#define GPIOD_SD_CD                 1
#define GPIOD_SD_CMD                2
#define GPIOD_PIN3                  3
#define GPIOD_PIN4                  4
#define GPIOD_SER_OUT_2             5
#define GPIOD_SER_IN_2              6
#define GPIOD_BARO_CS               7
#define GPIOD_LG_ACCEL_INT2         8
#define GPIOD_LG_ACCEL_INT1         9
#define GPIOD_LG_ACCEL_CS           10
#define GPIOD_PIN11                 11
#define GPIOD_PIN12                 12
#define GPIOD_SJ1                   13
#define GPIOD_PIN14                 14
#define GPIOD_PIN15                 15

#define GPIOE_MAGNO_DRDY            0
#define GPIOE_PIN1                  1
#define GPIOE_PIN2                  2
#define GPIOE_PIN3                  3
#define GPIOE_PIN4                  4
#define GPIOE_PIN5                  5
#define GPIOE_PIN6                  6
#define GPIOE_PYRO_1_C              7
#define GPIOE_PYRO_2_C              8
#define GPIOE_PYRO_3_C              9
#define GPIOE_PYRO_1_F              10
#define GPIOE_PYRO_2_F              11
#define GPIOE_PYRO_3_F              12
#define GPIOE_GYRO_INT1             13
#define GPIOE_GYRO_DRDY             14
#define GPIOE_PIN15                 15

#define GPIOF_PIN0                  0
#define GPIOF_PIN1                  1
#define GPIOF_PIN2                  2
#define GPIOF_PIN3                  3
#define GPIOF_PIN4                  4
#define GPIOF_PIN5                  5
#define GPIOF_PIN6                  6
#define GPIOF_PIN7                  7
#define GPIOF_PIN8                  8
#define GPIOF_PIN9                  9
#define GPIOF_PIN10                 10
#define GPIOF_PIN11                 11
#define GPIOF_PIN12                 12
#define GPIOF_PIN13                 13
#define GPIOF_PIN14                 14
#define GPIOF_PIN15                 15

#define GPIOG_PIN0                  0
#define GPIOG_PIN1                  1
#define GPIOG_PIN2                  2
#define GPIOG_PIN3                  3
#define GPIOG_PIN4                  4
#define GPIOG_PIN5                  5
#define GPIOG_PIN6                  6
#define GPIOG_PIN7                  7
#define GPIOG_PIN8                  8
#define GPIOG_PIN9                  9
#define GPIOG_PIN10                 10
#define GPIOG_PIN11                 11
#define GPIOG_PIN12                 12
#define GPIOG_PIN13                 13
#define GPIOG_PIN14                 14
#define GPIOG_PIN15                 15
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

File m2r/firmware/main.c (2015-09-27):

/*
 * M2R
 * 2014 Adam Greig, Cambridge University Spaceflight
 */

#include <stdio.h>
#include <string.h>

#include "ch.h"
#include "hal.h"

#include "sbp_io.h"
#include "ublox.h"
#include "radio.h"
#include "dispatch.h"
#include "rockblock.h"
#include "m2r_shell.h"
#include "m2serial.h"
#include "m2status.h"

static WORKING_AREA(waThreadHB, 128);
static WORKING_AREA(waThreadUblox, 4096);
static WORKING_AREA(waThreadRadio, 2048);
static WORKING_AREA(waM2Serial, 1024);
static WORKING_AREA(waM2Status, 1024);
/*static WORKING_AREA(waThreadSBP, 2048);*/
static WORKING_AREA(waDispatch, 1024);

static msg_t ThreadHeartbeat(void *arg) {
    (void)arg;
    chRegSetThreadName("heartbeat");

    while (TRUE) {
        palSetPad(GPIOB, GPIOB_LED_STATUS);
        palSetPad(GPIOB, GPIOB_BUZZER);
        IWDG->KR = 0xAAAA;

        if(/*M2FCBodyStatus.m2fcbody == STATUS_OK &&*/
           M2FCNoseStatus.m2fcnose == STATUS_OK)
        {
            chThdSleepMilliseconds(50);
        } else {
            chThdSleepMilliseconds(500);
        }

        palClearPad(GPIOB, GPIOB_LED_STATUS);
        palClearPad(GPIOB, GPIOB_BUZZER);
        IWDG->KR = 0xAAAA;
        chThdSleepMilliseconds(500);
    }
    return (msg_t)NULL;
}

int main(void) {
    halInit();
    chSysInit();
    chRegSetThreadName("main");

    LocalStatus = &M2RStatus;

    /*sbp_state_init(&sbp_state);*/
    rockblock_init();
    dispatch_init();

    chThdCreateStatic(waThreadHB, sizeof(waThreadHB), LOWPRIO,
                      ThreadHeartbeat, NULL);

    /* Configure and enable the watchdog timer, stopped in debug halt */
    DBGMCU->APB1FZ |= DBGMCU_APB1_FZ_DBG_IWDG_STOP;
    IWDG->KR = 0x5555;
    IWDG->PR = 3;
    IWDG->KR = 0xCCCC;

    m2serial_shell = m2r_shell_run;
    M2SerialSD = &SD2;
    chThdCreateStatic(waM2Serial, sizeof(waM2Serial), HIGHPRIO,
                      m2serial_thread, NULL);

    chThdCreateStatic(waM2Status, sizeof(waM2Status), HIGHPRIO,
                      m2status_thread, NULL);

    chThdCreateStatic(waThreadUblox, sizeof(waThreadUblox), NORMALPRIO,
                      ublox_thread, NULL);

    chThdCreateStatic(waThreadRadio, sizeof(waThreadRadio), NORMALPRIO,
                      radio_thread, NULL);

    chThdCreateStatic(waDispatch, sizeof(waDispatch), NORMALPRIO,
                      dispatch_thread, NULL);

    chThdSetPriority(LOWPRIO);
    chThdSleep(TIME_INFINITE);

    return 0;
}

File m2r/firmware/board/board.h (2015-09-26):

/*
 * M2R ChibiOS Board definition file.
*/

#ifndef _BOARD_H_
#define _BOARD_H_

/*
 * Board identifier.
 */
#define BOARD_M2R
#define BOARD_NAME                  "M2R"


/*
 * Board oscillators-related settings.
 */
#if !defined(STM32_LSECLK)
#define STM32_LSECLK                0
#endif

#if !defined(STM32_HSECLK)
#define STM32_HSECLK                8000000
#endif

/*
 * Board voltages.
 * Required for performance limits calculation.
 */
#define STM32_VDD                   330

/*
 * MCU type as defined in the ST header.
 */
#define STM32F30X

/*
 * IO pins assignments.
 */
#define GPIOA_PIN0                  0
#define GPIOA_5VOUT                 1
#define GPIOA_SER_OUT               2
#define GPIOA_SER_IN                3
#define GPIOA_MTX2_TXD              4
#define GPIOA_BAT_MON               5
#define GPIOA_LED_A                 6
#define GPIOA_LED_C                 7
#define GPIOA_NRST                  8
#define GPIOA_RB_RX                 9
#define GPIOA_RB_TX                 10
#define GPIOA_PIN11                 11
#define GPIOA_PIN12                 12
#define GPIOA_SWDIO                 13
#define GPIOA_SWCLK                 14
#define GPIOA_PIN15                 15

#define GPIOB_PIN0                  0
#define GPIOB_MTX2_P0               1
#define GPIOB_MTX2_P1               2
#define GPIOB_PIN3                  3
#define GPIOB_PIN4                  4
#define GPIOB_PIN5                  5
#define GPIOB_GPS_SCL               6
#define GPIOB_GPS_SDA               7
#define GPIOB_GPS_RESET             8
#define GPIOB_BUZZER                9
#define GPIOB_MTX2_EN               10
#define GPIOB_PIN11                 11
#define GPIOB_LED_RADIO             12
#define GPIOB_LED_RB                13
#define GPIOB_LED_GPS               14
#define GPIOB_LED_STATUS            15

#define GPIOC_PIN0                  0
#define GPIOC_PIN1                  1
#define GPIOC_PIN2                  2
#define GPIOC_PIN3                  3
#define GPIOC_PIN4                  4
#define GPIOC_PIN5                  5
#define GPIOC_PIN6                  6
#define GPIOC_PIN7                  7
#define GPIOC_PIN8                  8
#define GPIOC_PIN9                  9
#define GPIOC_PIN10                 10
#define GPIOC_PIN11                 11
#define GPIOC_PIN12                 12
#define GPIOC_PIN13                 13
#define GPIOC_PIN14                 14
#define GPIOC_PIN15                 15

#define GPIOD_OSCIN                 0
#define GPIOD_OSCOUT                1
#define GPIOD_PIN2                  2
#define GPIOD_PIN3                  3
#define GPIOD_PIN4                  4
#define GPIOD_PIN5                  5
#define GPIOD_PIN6                  6
#define GPIOD_PIN7                  7
#define GPIOD_PIN8                  8
#define GPIOD_PIN9                  9
#define GPIOD_PIN10                 10
#define GPIOD_PIN11                 11
#define GPIOD_PIN12                 12
#define GPIOD_PIN13                 13
#define GPIOD_PIN14                 14
#define GPIOD_PIN15                 15

#define GPIOE_PIN0                  0
#define GPIOE_PIN1                  1
#define GPIOE_PIN2                  2
#define GPIOE_PIN3                  3
#define GPIOE_PIN4                  4
#define GPIOE_PIN5                  5
#define GPIOE_PIN6                  6
#define GPIOE_PIN7                  7
#define GPIOE_PIN8                  8
#define GPIOE_PIN9                  9
#define GPIOE_PIN10                 10
#define GPIOE_PIN11                 11
#define GPIOE_PIN12                 12
#define GPIOE_PIN13                 13
#define GPIOE_PIN14                 14
#define GPIOE_PIN15                 15

#define GPIOF_PIN0                  0
#define GPIOF_PIN1                  1
#define GPIOF_PIN2                  2
#define GPIOF_PIN3                  3
#define GPIOF_PIN4                  4
#define GPIOF_PIN5                  5
#define GPIOF_PIN6                  6
#define GPIOF_PIN7                  7
#define GPIOF_PIN8                  8
#define GPIOF_PIN9                  9
#define GPIOF_PIN10                 10
#define GPIOF_PIN11                 11
#define GPIOF_PIN12                 12
#define GPIOF_PIN13                 13
#define GPIOF_PIN14                 14
#define GPIOF_PIN15                 15
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

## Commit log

2014-05-06 first go at schematic
    [m2p.sch]
2014-05-08 m2p sch looking good
    [m2p.sch]
2014-05-08 reorganise repo a little
    [m2p.sch, m2r.sch]
2014-05-08 reorganise some more
    [m2p.sch, m2r.sch]
2014-05-08 add battery voltage monitoring
    [m2p.sch]
2014-05-09 swap to an STM32 chip
    [m2p.sch]
2014-05-09 annotate parts
    [m2p.sch]
2014-05-09 fix a few typos
    [m2p.sch]
2014-05-09 rearrange LEDs a little
    [m2p.sch]
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2014-05-09 respec parts for stock level
    [m2p.sch]
2014-05-09 stm32 is lqfp package
    [m2p.sch]
2014-05-09 add power flags so ERC all pass
    [m2p.sch]
2014-05-09 add part number for ic2
    [m2p.sch]
2014-05-09 put LED on JNTRST instead of continuity measure
    [m2p.sch]
2014-05-19 place most major parts for m2r
    [m2r.sch]
2014-05-20 add first go at m2r schematic
    [m2p.sch, m2r.sch]
2014-05-20 spec crystal part
    [m2r.sch]
2014-05-20 swap STM32F103 for STM32F303
    [m2r.sch]
2014-05-22 finish up m2r schematic
    [m2p.sch, m2r.sch]
2014-05-22 use two 100R to make up 50R because lol
    [m2r.sch]
2014-05-22 swap 50R to two 100R on m2p too
    [m2p.sch]
2014-05-22 oops, annotate
    [m2p.sch]
2014-05-27 Add second connector for arming switch to m2r
    [m2r.sch]
2014-05-27 add separate connector for arming switch to m2p
    [m2p.sch]
2014-05-27 Change F103 to F303 on m2p
    [m2p.sch]
2014-05-29 swap SP100-2T for MS5611-01BA03 barometer
    [m2p.sch, m2r.sch]
2014-05-29 add farnell number for new barometer
    [m2p.sch, m2r.sch]
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2014-05-30 add most of the libraries m2d'l probs want
    [m2d.sch]
2014-06-19 make a good start on m2d schematic
    [m2d.sch, m2r.sch]
2014-07-02 swap to f415, reorg sch into sheets, spec strain gauge Rg
    [imu.sch, io.sch, m2d.sch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]
2014-07-05 rename m2d to m2fc which now incorporates m2p
    [imu.sch, io.sch, m2fc.sch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]
2014-07-09 update more bits on flight computer..
    [imu.sch, io.sch, m2fc.sch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]
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2014-07-10 fix all the erc errors
    [imu.sch, io.sch, m2fc.sch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]
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2014-07-10 add missing farnell numbers
    [imu.sch, thermocouples.sch]
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2014-07-10 further wibbling about things
    [m2r.sch, straingauges.sch]
2014-07-10 something went weird with mtx2 footprint, redo
    [m2r.sch]
2014-07-18 update m2fc sch with 3rd pyro and SJs
    [imu.sch, io.sch, m2fc.sch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]
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2014-07-20 swap to JST PA range connectors
    [io.sch, m2fc.sch, m2r.sch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]
2014-07-21 rejig m2r schematic a little for i2c gps
    [m2r.kicad_pcb, m2r.sch, straingauges.sch]
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2014-07-22 a good looking ratsnest
    [m2r.kicad_pcb, m2r.sch]
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2014-07-22 further pcb work i guess
    [m2r.kicad_pcb, m2r.sch]
2014-07-23 2 airwires to go
    [m2r.kicad_pcb, m2r.sch]
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2014-07-23 gps top gnd plane
    [m2r.kicad_pcb]
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2014-07-23 no paste on sjs, tps, ants
    [m2r-B_Cu.gbl, m2r-B_Mask.gbs, m2r-B_SilkS.gbo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]
2014-07-23 changed ESD diode to 12V one
    [m2r-B_Cu.gbl, m2r-B_Mask.gbs, m2r-B_SilkS.gbo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]
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2014-07-24 quick go at wiring diagram
    [m2fc.sch, m2r.kicad_pcb, straingauges.sch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]
2014-07-24 change alm silk, bottom mask on sma, add better gnd track to rb
    [m2r-B_Cu.gbl, m2r-B_Mask.gbs, m2r-B_SilkS.gbo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]
2014-07-24 sd pullups, shielded sgs
    [imu.sch, io.sch, m2fc.kicad_pcb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]
2014-07-28 add esd diodes to m2fc
    [imu.sch, io.sch, m2fc.kicad_pcb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]
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2014-07-30 m2fc footprints, start layout
    [imu.sch, io.sch, m2fc.farnell_spread.csv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]
2014-07-30 layout going ok so far...
    [io.sch, m2fc.kicad_pcb, m2fc.sch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]
2014-07-30 about to do something dangerous to pcb
    [m2fc.kicad_pcb]
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2014-07-30 swap crystal to smt. ready 2 route!!
    [m2fc.farnell_spread.csv, m2fc.kicad_pcb, m2fc.sch]
2014-07-30 analogue section routed woop woop
    [m2fc.kicad_pcb]
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2014-07-31 flip around power connectors
    [io.sch, m2fc.kicad_pcb, m2fc.sch]
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2014-07-31 ready to go go go
    [imu.sch, io.sch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]
2014-08-01 final checks, tweaks, etc
    [imu.sch, io.sch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]
2014-08-01 oh actually regen inner copper 2 and reship
    [m2fc-B_Cu.gbl, m2fc-B_Mask.gbs, m2fc-B_SilkS.gbo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]
2014-08-06 spec alt part for m2r 10p capacitor
    [m2r.sch]
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2014-08-17 change sd card part number on m2fc
    [m2fc.sch]
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2014-09-09 add drawings for jack and further m2fc fw bist
    [m2fc-Edge_Cuts.dxf, m2fc-NPTH-drl_map.dxf, m2fc-drl_map.dxf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]
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2015-05-20 add m2r r2 schematic
    [m2r.kicad_pcb, m2r.sch]
2015-05-20 remove unused libraries from m2r-r2 sch
    [m2r.sch]
2015-05-20 remove old m2r pcb
    [m2r.kicad_pcb]
2015-05-21 almost all m2r r2 routed except vcc lol
    [m2r.kicad_pcb, m2r.sch]
2015-05-23 finished up routing, done silk
    [m2r-B_Cu.gbl, m2r-B_Mask.gbs, m2r-B_SilkS.gbo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]
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2015-05-25 make case-size version of M2PA
    [m2pa-B_Cu.gbl, m2pa-B_Mask.gbs, m2pa-B_SilkS.gbo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]
2015-05-26 add tiny version for diecast case
    [m2pa-instrument.kicad_pcb, m2pa-m3mount.kicad_pcb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]
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2015-06-29 add pinout to bottom silk on m2r-r2
    [m2r-B_Cu.gbl, m2r-B_Mask.gbs, m2r-B_SilkS.gbo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]
2015-06-29 try and model m2pa in box..
    [1590hf.fcstd, 1590hf.stp, assy.fcstd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]
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2015-07-22 add potential m2r cover design
    [emblem_path.dxf, m2r-r2.dxf]
2015-07-22 add boms/zips for manufacture
    [m2pa.fcstd, m2r.sch, power.fcstd]
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2015-07-22 add dxf laser cut covers for m2fc/m2rl
    [m2fc.dxf, m2rl.dxf]
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2015-08-14 further work but no real improvements
    [m2rl.dxf]
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2015-08-20 fixed some error in the code: Still an error on initilising gptConGrp, but mainly OK
    [halconf.h, main.c]
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2015-09-06 set the microsd log buffer a little smaller to avoid overfilling CCM
    [microsd.c]
2015-09-06 rescue symbols from m2fc pcb
    [imu.sch, io.sch, m2fc.sch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]
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2015-09-07 Fixed a bug in DMA conflict
    [hmc5883l.c, ms5611.c]
2015-09-08 Did some changes to most of the code, added some global variables for the shell to read, might be a good idea to check if that creates some problems
    [adxl3x5.c, hmc5883l.c, l3g4200d.c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]
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2015-09-19 Fix high pressure bug in state_estimation.c
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2015-09-19 check in example config files
    [body_config.txt, nose_config.txt]
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2015-09-19 fix typo in hmc5883l function name
    [hmc5883l.c]
2015-09-19 fix DMA allocations to minimise conflicts
    [mcuconf.h]
2015-09-19 add own spi_select etc for ms5611 to work around mutex issue
    [ms5611.c]
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2015-09-19 have main alt be m AGL not m ASL
    [body_config.txt, nose_config.txt]
2015-09-19 Add some manufacturing files from laptop
    [m2fc.dxf, m2pa-tiny-F_Paste.dxf, m2r-F_Paste.dxf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]
2015-09-20 have magno and gyro be config-controllable
    [body_config.txt, nose_config.txt]
2015-09-23 also use m2status for error reporting
    [adxl3x5.c]
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2015-09-24 move m2rl code into its own folder
    [m2rl-F_Paste.dxf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]
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
